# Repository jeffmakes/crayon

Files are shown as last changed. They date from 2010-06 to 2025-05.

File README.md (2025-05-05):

# Crayon
This project explores the possibility of making prototype PCB's by inkjet printing wax as an etch resist.

Check out [a talk](https://media.ccc.de/v/27c3-4099-en-file_print_electronics) I gave about the project at 27C3.

The whole printer
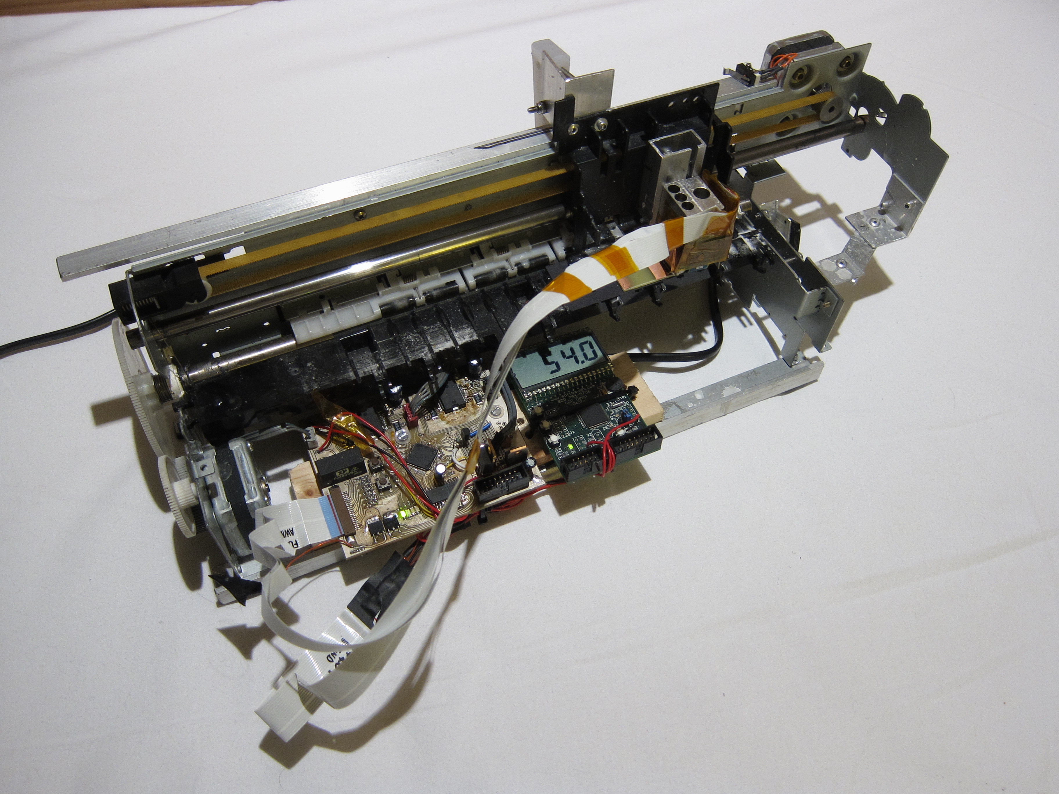
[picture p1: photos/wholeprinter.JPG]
The whole printer


Results
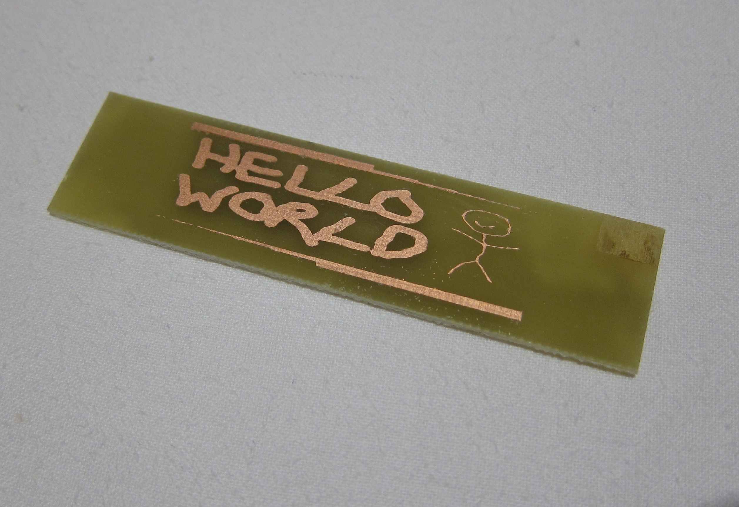
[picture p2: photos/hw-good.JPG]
Results


# Licence
The hardware designs are licensed under the CERN Open Hardware Licence Version P.
The firmware files are licensed under the MIT Licence.

# System Overview

## Motion Platform

Crayon is built on the chassis of a very old inkjet printer. It's old enough to use stepper motors for both the carriage axis and media feed axis.

## Printhead Assembly

The printhead from an Epson Stylus S21 was chosen for printing the wax. It is mounted to a custom machined heated reservoir block to hold and melt the wax. The original drive electronics from the S21 was reverse engineered, allowing a custom print controller board to be built.

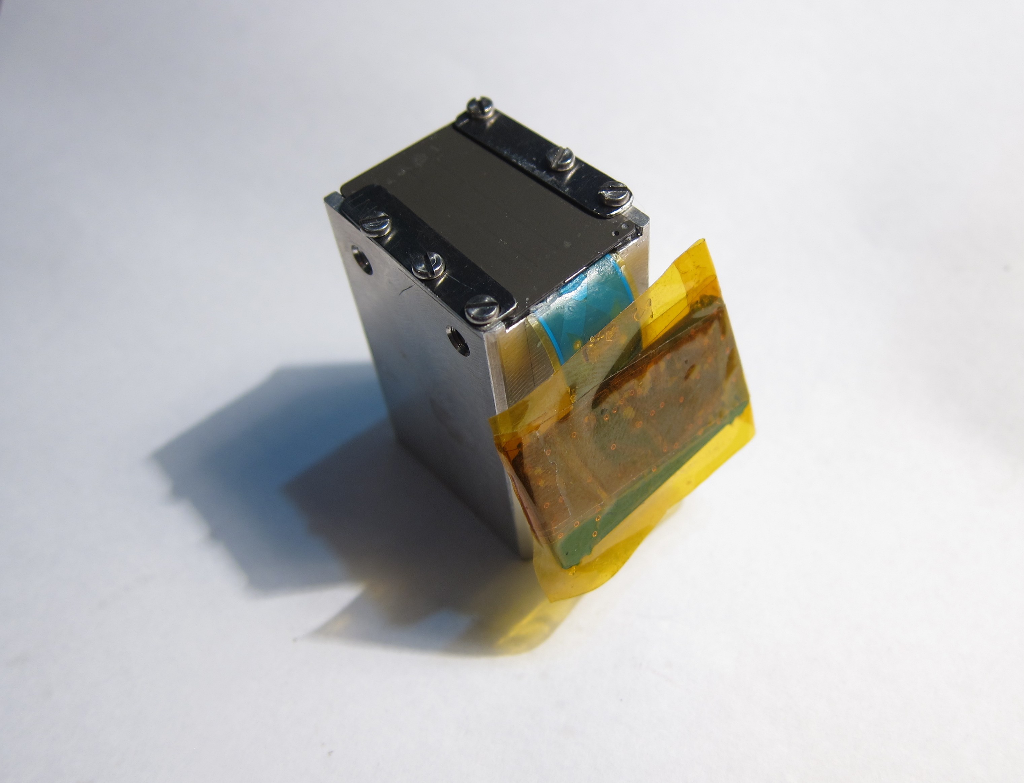
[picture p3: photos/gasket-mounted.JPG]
Printhead


## Heater

A custom heater PCB heats the reservoir block with a power transistor. A MSP430F437 microcontroller development board runs a PID control algorithm to set the temperature, and displays it on an LCD.

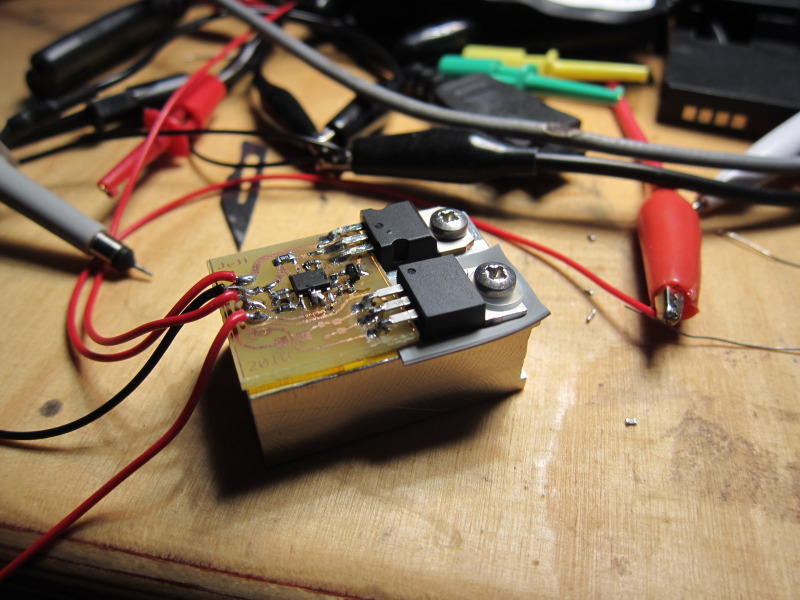
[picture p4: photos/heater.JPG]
Heater


## Controller

The heart of the printer is a custom controller PCB that generates the print data and drive waveforms for the printhead, and drives the stepper motors in the motion platform. It is based on an MSP430F2618 microcontroller. The controller is a complete replacement for the one in the Stylus S21 - the printhead interface has been completely reverse engineered, permitting full control of the printing parameters. 

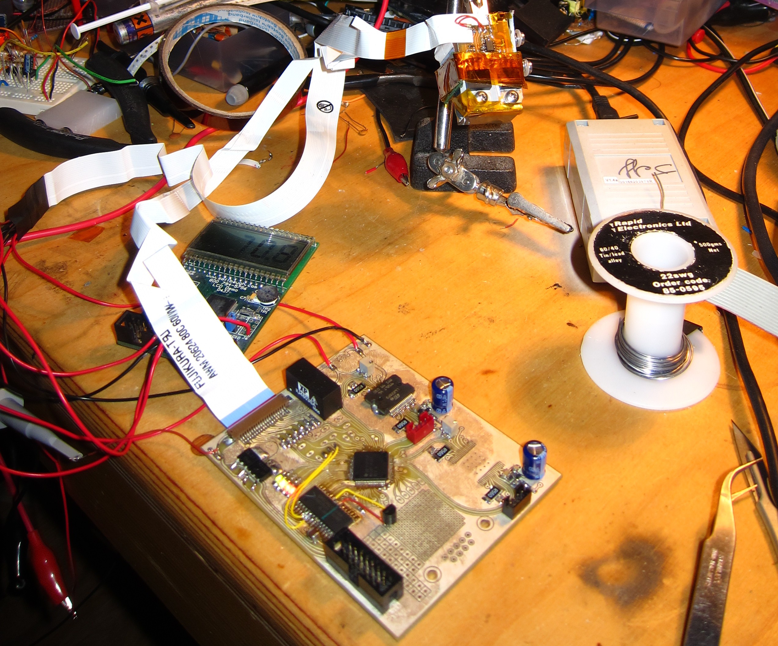
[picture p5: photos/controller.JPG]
Controller


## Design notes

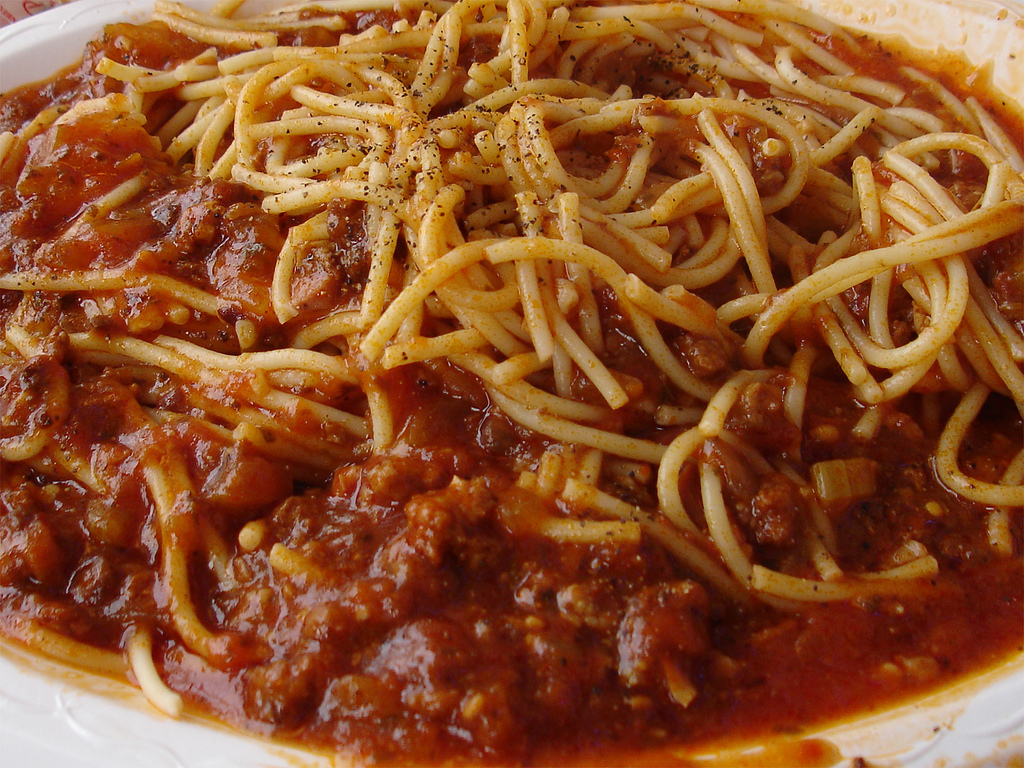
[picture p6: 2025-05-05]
photos/spaghetti.jpg

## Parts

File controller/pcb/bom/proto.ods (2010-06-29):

Part | Qty | Farnell | Description
IC1 | 1 |  | MSP430F2618TPN
IC3 | 2 | 1271000 | L6228PD Bipolar stepper Driver
D1, D2 | 4 | 1466524 | Diode 1N4148WS

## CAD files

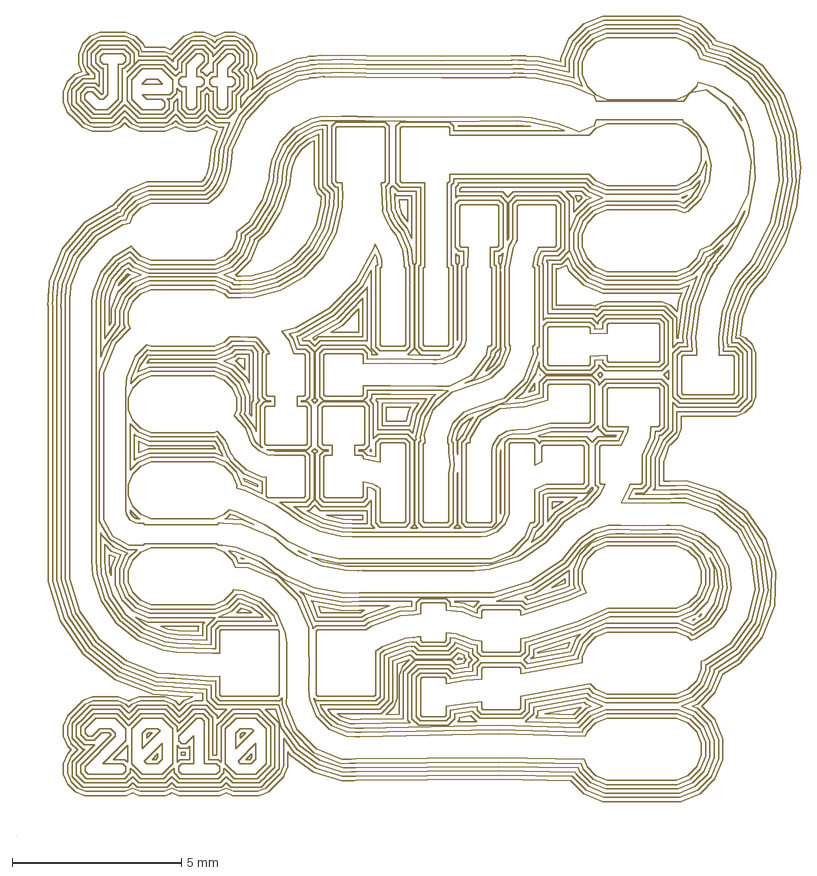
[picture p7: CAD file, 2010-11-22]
heater/pcb/heatertop.dxf
23.1 x 24.2 mm

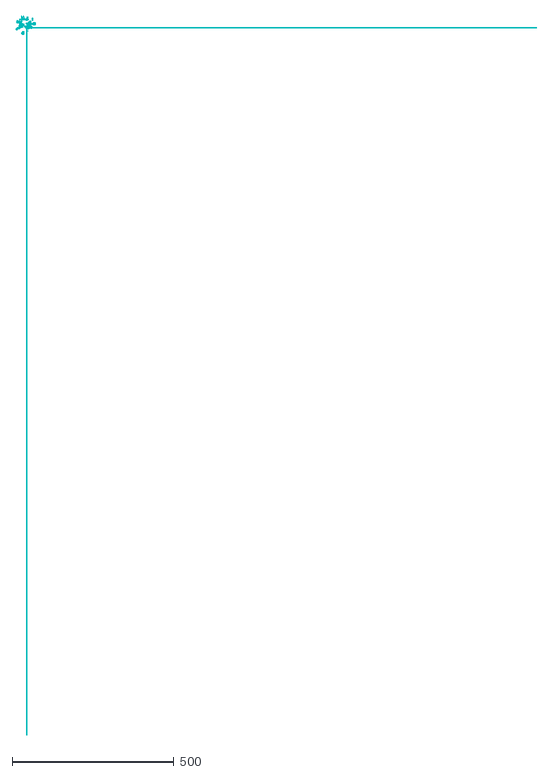
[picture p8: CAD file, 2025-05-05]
printhead-mech/paste-ungrouped.dxf
1606.8 x 2221.3

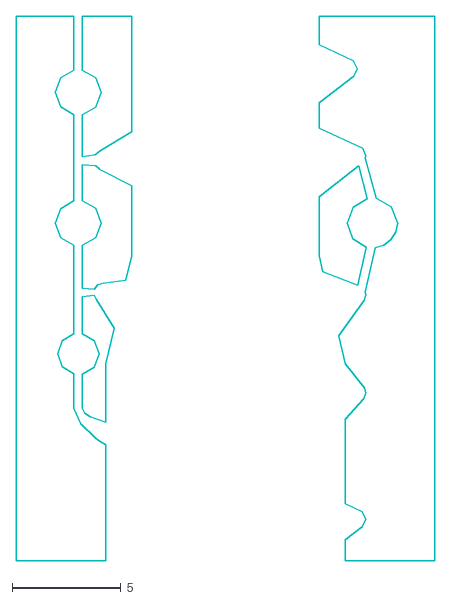
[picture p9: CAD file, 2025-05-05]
printhead-mech/gasket-mask-mirrored-2.dxf
19.2 x 25.0

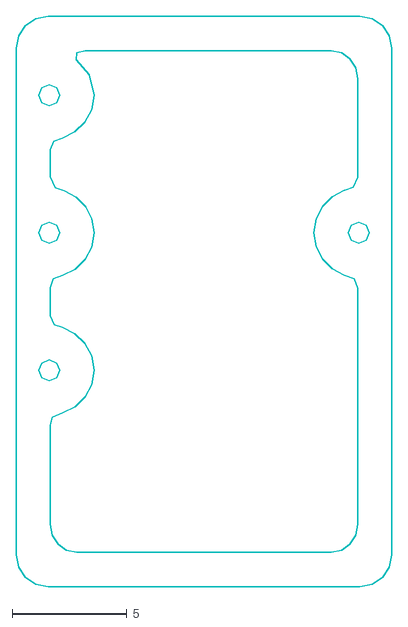
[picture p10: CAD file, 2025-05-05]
printhead-mech/rubber-gasket.dxf
16.4 x 24.9

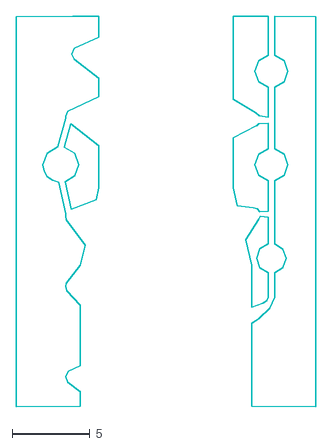
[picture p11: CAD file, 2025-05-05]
printhead-mech/gasket-mask-mirrored-3.dxf
19.2 x 25.0

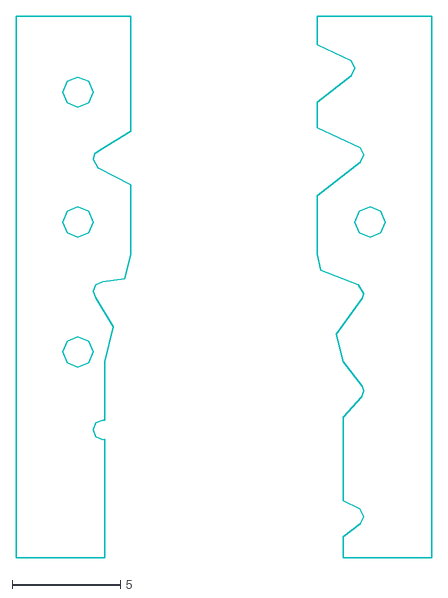
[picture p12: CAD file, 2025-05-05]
printhead-mech/tape-mk2.dxf
19.2 x 25.0

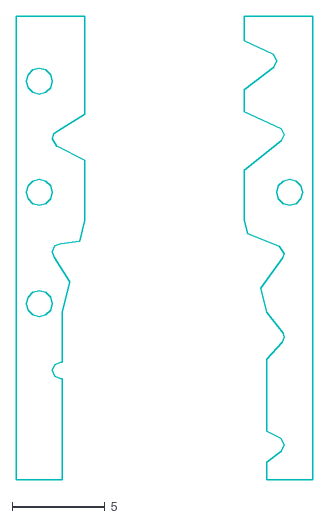
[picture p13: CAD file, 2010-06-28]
printhead-mech/tape.dxf
16.0 x 25.0

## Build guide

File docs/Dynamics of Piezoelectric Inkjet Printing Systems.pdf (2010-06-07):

# Dynamics of Piezoelectric Inkjet Printing Systems

## Shinri Sakai SEIKO EPSON Corporation Shiojiri, Nagano, Japan

### Abstract

In recent years, the inkjet technology has made great strides in the print quality. By introducing fine droplets, deep and light color inks, optimized media, and advanced color and image processing, the latest inkjet printers can produce photo-quality prints. Of these many improvements, the most contributive one is that the innovative piezoelectric print head has reduced the ink droplet size by a factor of ten in the latest five years. This innovation has been accomplished by optimizing head dimensions and driving signals as well as improving the manufacturing and assembling process. The piezoelectric actuator driven by the signal, optimized for the particular print head model, can precisely control the unrestrained ink meniscus vibration at the nozzle openings to achieve multi-sized droplets ejection in a sequent manner as well as stabilized droplet ejection up to the extremely high ejection repetition frequency. This Variable-Sized Droplet Technology (VSDT) has made it possible to introduce the digital photo-printers to the market without trading off the throughput. This paper shows how the piezoelectric inkjet technology has been improved and how much flexibility it has for particular use in home, office and industry.

### Introduction

Today, the inkjet technology has made it possible to produce high quality digital photo prints that compete against the silver halide photographs by the cooperation between the improvements of the components that constitute the inkjet technology [1] and to extend its application to wide and pioneering area by its compatibility and flexibility with digital sources.
Two types of the inkjet head technologies, one is using piezoelectric actuators and the other is using heater elements, are well known in the market. Because they have different physics and mechanism, they also have been taking different approaches to producing fine droplets. Figure 1 shows the history of the ink droplet size reduction achieved by the EPSON’s inkjet printers since its first market model in 1984. Throughout the evolution of the piezoelectric print heads, EPSON faced several difficulties in the development. Two innovative MACH technologies broke through the difficulties in 1992 and 1995 and made it possible to continue to make the successful progress. As is shown in Figure 1, the minimum droplet volume has been reduced every year and now reached 3pl. This rapid and drastic evolution, that reduced the ink droplet size by the factor of ten in the latest five years and still continues, have been making revolutions in the printing technology.
This paper will describe the structure of the inkjet heads, the dynamics of the heads, the basic approaches to generating fine droplets, and the multi-sized droplet technology accomplished by precisely controlling ink motion of the EPSON’s piezo-type inkjet printers. The application area of the piezo-type head will also be

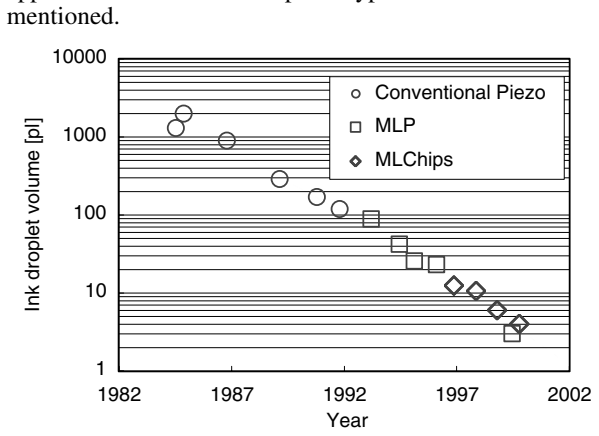
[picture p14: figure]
mentioned.; Year; Ink droplet volume [pl]; Conventional Piezo; MLP; MLChips

Figure 1. History of ink droplet volume of EPSON’s piezo type printers.

### Structure of the Piezoelectric Print Head

The piezoelectric inkjet head has a mechanism that transfers piezostriction to a volume change of the pressure chamber and this volume change induces oscillating ink flow that generates droplets from a nozzle opening. There are several types of the piezoelectric inkjet heads in terms of the mechanism of the piezo transducer.

Conventional Piezo Head
The early models since 1984 used piezo transducers similar to the head in the reference [2]. Each pressure chamber, sealed by a thin elastic plate, has a piezo strip that

IS&Ts NIP16: 2000 International Conference on Digital Printing Technologies

IS&Ts NIP16: 2000 International Conference on Digital Printing Technologies | Copyright 2000, IS&T

is narrower than the chamber width. The unimorph actuator (or vibration plate), composed of the laminate of the piezo strip and the elastic plate, transfers piezostriction to flexural deformation of the vibration plate. Figure 2 shows a plane view of the head of this type. The nozzles in a line are connected to the pressure chambers placed with large space by the long and winding channels. The manufacturing process, that puts and glues the each piezo strip on the channel substrate of plastic or glass, restricts the use of thin piezo elements thinner than about 100µm, because the piezo material is very brittle and easy to break in the process. As described later, this dimensional restriction limits the reduction of the droplets and the heads.

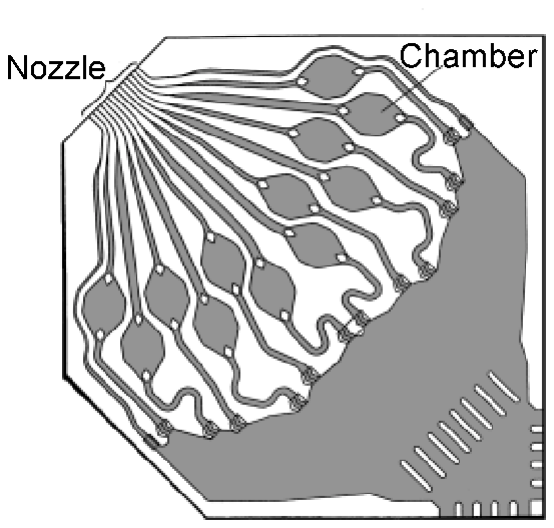
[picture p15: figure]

Figure 2. Conventional Piezo Head.

MLP (Multi-Layer Piezo) type MACH
To break through this limitation, EPSON developed new inkjet head with multi-layer piezo actuators called MLP type MACH (Multi-layer ACtuator Head), and introduced new printer with MACH in 1992 [3]. The MLP type MACH, shown in Figure 3, has multi-layer piezo elements sliced to thin pillar shape, one end of them is fixed to the base and the other end is connected to the vibration plates of the pressure chambers. This piezo element gets shorter to extend the pressure chamber by the transverse piezoelectric effect when voltage is supplied. Beside the unimorph actuator, the MLP actuator can transfer the piezostriction directly to the displacement of the vibration plate regardless of the pressure chamber size.

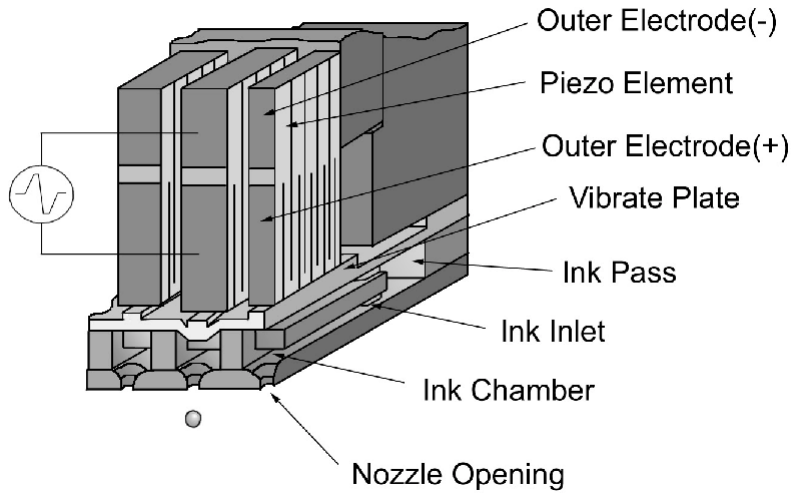
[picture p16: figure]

Figure 3. Structure of the MLP type MACH

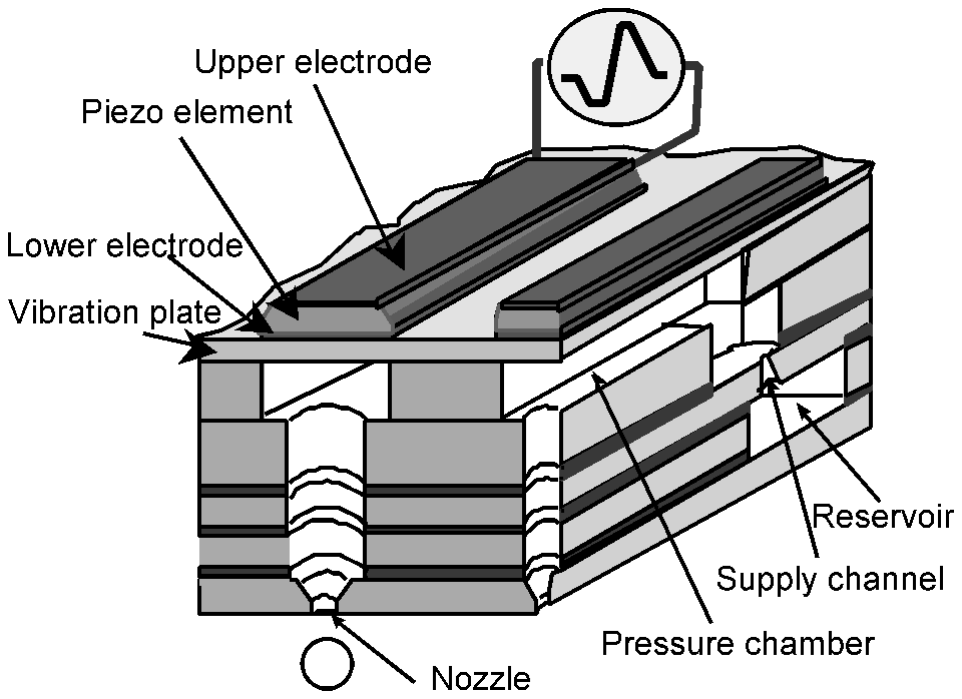
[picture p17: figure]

Figure 4. Structure of MLChips type MACH.

MLChips (Multi-Layer Ceramic with Hyper Integrated Piezo Segments) type MACH
While having high performance, the MLP type MACH costs a lot to be manufactured. To meet the market demand for low-cost and high performance inkjet printers, EPSON developed another MACH in 1995 [4]. Though the principle of the transducer, shown in Figure 4, is similar to the conventional piezo head, the piezo strips are not independently manufactured but processed and sintered together with the flow channel substrate as a single layered ceramics structure. As described later, it is strongly required to make both of the vibration plate and the piezo strip thinner to improve the inkjet head for jetting fine droplets. By taking the process that unifies the core parts of the head without machining and gluing, the MLChips could break the barrier, which the conventional piezo heads had, to develop the high cost performance printers by reducing the head dimensions.

### Dynamics of the Print Head

Understanding the motion of the actuator and the ensuing ink flow, which are actually coupled each other, and precisely estimating the parameters that define and characterize the motion, the accurate design can be done to meet the fine droplet target. In this section, the basic analytical models for the estimation of the inkjet head’s response will be explained and the responses to the simple basic inputs will be shown. Then, the relations between the analytical models and design parameters, and the strategies to the design for generating micro droplets will be described.

Analytical models for the piezoelectric inkjet heads
The channel flows that interact with the actuator as inkjet heads do are well explained by the acoustic model that takes volume velocity and pressure as independent variables. Each component of the inkjet head, such as nozzle, pressure chamber, and vibration plate, is expressed in terms of acoustic impedance, composed of inertance, compliance and acoustic resistance, and is put together in electric circuit as a equivalent model of the inkjet system. Figure 5 shows the simple equivalent circuit model for the MLChips type MACH, which uses unimorph actuator, and two major vibration modes. The mode in Figure 5(b) is the vibration mode of the pressure chamber connected to the compliance of the chamber that results in ink droplet ejection from the nozzle. The mode in Figure 5(c) is the vibration mode of the ink supply flow connected to the capillary force at the nozzle meniscus that manages the frequency characteristics of the droplet ejection.
Figure 6 shows the equivalent circuit model for the MLP type MACH. The longitudinal vibration actuator of MLP has high rigidity and can actuate the vibration plate forcibly. Add to the vibration modes of the pressure chamber (Figure 6(a)) and the ink supply flow (Figure 6(b)), there is the vibration mode of the MLP (Figure 6(c)).

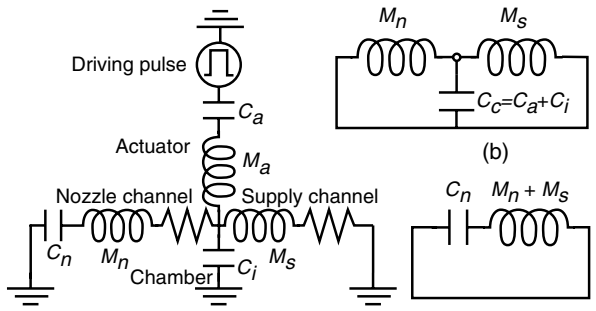
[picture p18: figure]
Nozzle channel; Supply channel; Chamber; Driving pulse; Actuator

(a) (c)

Figure 5. Equivalent model of the MLChip type MACH.

Cn Mn + Ms

Cc=Cv+Ci

Mn | Ms

(b)

(a) Ca

Ma

(c)

Figure 6. Equivalent model of the MLP type MACH.

Meniscus control
When a drive signal is applied to the piezo element, induced piezoelectric strain generates a driving force and excites the above mentioned vibration modes. Of these vibrations, the mode of the pressure chamber and its oscillation period Tc

determine the characteristics of ink ejection. Figure 7 shows the oscillating flow at the nozzle of MLChips type MACH connected to the vibration mode of the pressure chamber in response to a drive pulse of which width is the same as the oscillation period Tc

. Figure
8 shows the response to a negative drive pulse of which width is half of the Tc

(a)

0.5

1

V/Vh

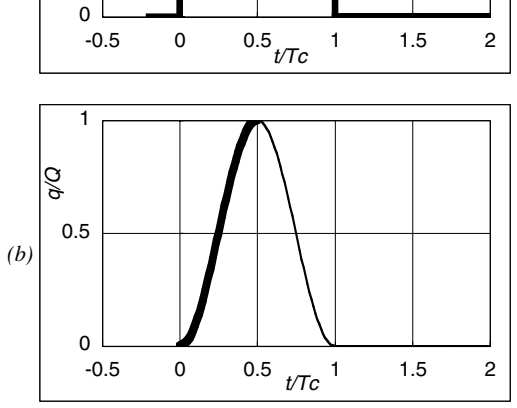
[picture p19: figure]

Figure 7. Push-Pull pulse (a) and response (b). Time in abscissa is normalized by Tc, and also voltage and flow quantity in ordinates are normalized by the pulse height and flow amplitude respectively.

The drive pulse shown in Figure 7 excites the ink oscillation that flows outward first at the preceding positive edge of the pulse, and pushes the ink at nozzle to generate a droplet. The following edge of the pulse excites the ink oscillation that flows inward first. As the following flow is in opposite phase to the preceding flow, i.e. out of phase, both flows cancel each other and no oscillation flow remains. This driving method is called Push-Pull operation. In the case of the drive pulse shown in Figure 8, the pulse width of that is half of the Tc

, an ink flow excited by
the preceding pulse (negative) edge starts to draw ink meniscus inward first, and at the time just when the ink flow begins to turn its flow direction, the following edge of the pulse generates another ink flow. Because these two ink oscillation flows are in phase, they reinforce each other, then construct a large oscillation flow, and generate a droplet twice as fast as the Push-Pull operation. This driving method is called Pull-Push operation.

(a)

0.5

1
V/Vh

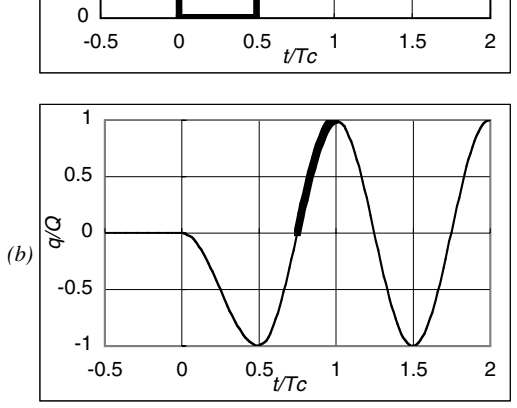
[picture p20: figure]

Figure 8. Pull-Push pulse (a) and response (b).
As well as the pulse width described above, rise-time or fall-time, in that time the pulse ramps up or down between two voltages, is also very important parameter. Compared with the sharp edge case, if the rise-time or fall-time is equal to the Tc

, no overshoot is observed in Figure 9. This pulse edge draws ink meniscus to some amount without any residual oscillations and is very useful for

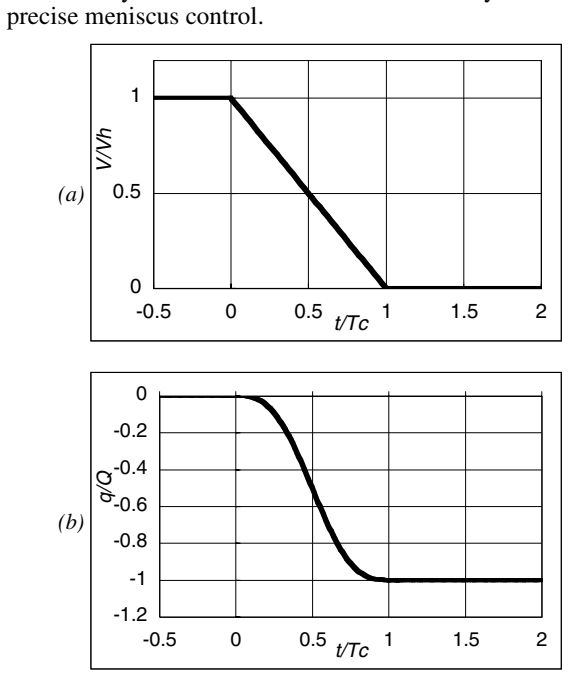
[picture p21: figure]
precise meniscus control.

Figure 9. Ramp step input (a) and response (b).

Approach to fine droplets generation
Generally, reducing the droplet volume causes slowing down the droplet speed. In the shuttle type inkjet printers, the inkjet head ejects droplets while moving fast, so the slower droplets degrade dots positioning accuracy and resultant image quality. Accordingly, the way to the faster droplets is exactly the way to the smaller droplets.
The droplet velocity is estimated by integrating ink momentum going out of the nozzle and then dividing the figure of the momentum by the droplet mass. In the case of the Push-Pull operation, integrating the flow, thick line in Figure 7, gets the droplet velocity Vm as

2
4 m
c

Q V
TA
π= | (1)

where Q is the droplet volume and A is the area of the nozzle aperture. And the oscillation period Tc

is
T | MC c | c = 2π | (2)

where Cc

is the compliance of the pressure chamber and M is total inertance of parallel connection of the nozzle and supply ink channels.
From Equation (1), the smaller the oscillation period Tc and nozzle become, the faster droplets eject. Although it helps the droplets to speed up, reducing the nozzle size causes clogging up of the nozzles, so it is difficult to make use of that. On the other hand, from Equation (2), the oscillation period Tc

is proportional to the square root of Cc

,
and as the Cc

is strongly influenced by the dimension of the vibration plate, reducing the chamber compliance is very effective to shorten the oscillation period Tc

In principle, the compliance of the vibration plate is proportional to the 5th power of the vibration plate width and is inversely proportional to the 3rd power of the plate thickness. Add to this, in the case of the MLChips type MACH, theoretically, the volume displacement of the vibration plate driven by the same voltage is proportional to the 3rd power of the width and is inversely proportional to the 2nd power of the thickness.
By optimizing both width and thickness of the vibration plate, i.e. reducing both width and thickness, for the specific droplet size, the consistent design with the evolution of the droplet size can be made.

### Multi-Sized Droplet Technology

It is evident that small droplets size needs the large number of droplets to cover the whole media with ink. But the piezoelectric inkjet head is difficult to reduce the nozzle spacing and increase the number of nozzle in terms of cost. So if only the reduction of the droplet size is made, the print head would have to shuttle lots of times and this would result in a large drop in the throughput.
The MSDT (Multi-Sized Droplet Technology) can overcome this difficulty, ejecting differently sized ink droplets in one scanning. The number of scanning is defined by the largest droplet size the head can eject, not by the smallest.
Figure 10 shows the MSDT applied to MLP type MACH [5]. The pulse pattern from the common pulse generator, applied to each piezo transducer, has two driving pulses in one cycle, corresponding to the pixel grid point. When the switch of the piezo transducer selects the pulse part2, small droplet of 3pl would eject and form a small dot (Figure 10[C]). When the pulse part3 is selected, large droplet of 10pl would eject and form a middle dot (Figure 10[D]). In the case that both pulses are selected, the large droplet would be larger than the case D by the effect of the preceding small dot ejection, two droplets would eject and total ink volume of 19pl would form a large dot (Figure 10[E]).
In the MSDT, the drive waveform is designed so that the droplets with different sizes would have about the same velocity. While the simple Pull-Push operation would eject droplets twice as fast as the Push-Pull operation, by taking large Pull and small Push, the smaller droplet ejection was made possible.
Also in the MSDT, new idea of the Pull-Push-Pull operation, which is the combination of the Pull-Push and the Push-Pull, is implemented. The last Pull is set to cancel the previously generated flow like the Push-Pull operation. The response to this complex waveform can be easily understood by the superposition of the oscillations generated by each pulse edge.

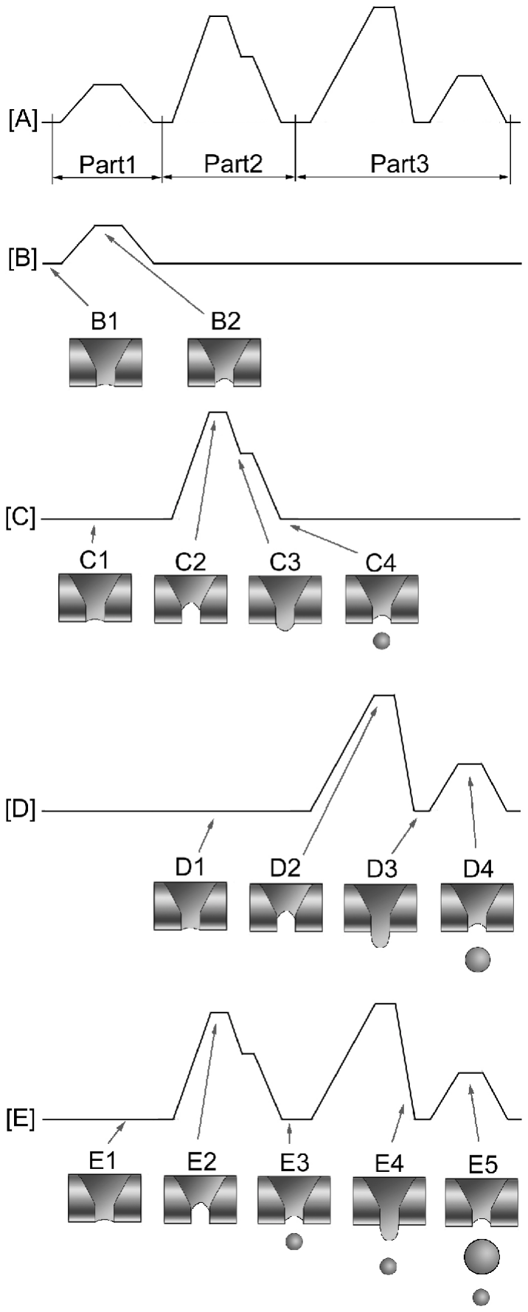
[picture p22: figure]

Figure 10. Driving waveform of MSDT

### Evolution of the Piezo Inkjet Technology

As above described, the piezoelectric inkjet head can precisely control the ink meniscus motion and change the droplet volume by means of the driving signal. This controllability made possible to adapt the inkjet heads to plenty of ink and media combinations and apply them to from the photo quality home print to the professional large format and arts.
From the viewpoint of the droplet size, if only a small droplet is pursued, it is easy to establish a new record. On the other hand, piezoelectric inkjet head can accept a variety of inks other than water base inks. These potentials can lead the piezo inkjet head to the new application area of the marking technology.

### Conclusion

The piezoelectric inkjet heads has been evolving at marvelous speed, introducing new actuators. The high linearity of the actuators has given the high controllability, and the design flexibility and ultimate optimizing technique established applicability of the piezo inkjet technology to the all sort of digital printings.

### References

1. M. Fujino, Proc. SPIE, Vol. 3963, pp. 340-348 (2000).
2. E. L. Kyser, S. B. Sears, US patent 3,946,398, (1976).
3. | T. Kitahara, Proc. IS&T’s 11th | International Congress on
Advances in Non-Impact Printing Technologies, pp. 346-349
| (1995).
4. | M. Usui, Proc. IS&T’s 12th | International Conference on
Digital Printing Technologies, (1996).
5. T. Kitahara, Japan Hardcopy ‘99, pp. 335-338 (1999).

### Biography

Shinri Sakai is a chief specialist in the Printer Development Division of SEIKO EPSON Corporation. He received his B.E. and M.E. in mechanical engineering from the Tokyo Institute of Technology, Japan, in 1983 and 1985 respectively. He worked on electrophotography system for three years and currently is working on ink jet printing system development. His primary responsibilities are mechanical and physical analysis and computer simulation for ink jet head development and optimization. His recent interests are rheological features of inks and their contribution to ink meniscus control and droplet formation.

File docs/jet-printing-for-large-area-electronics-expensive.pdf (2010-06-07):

# Jet Printing for Large Area Electronics

## Steven Ready, William Wong, Kateri Paul, and Bob Street

Palo Alto Research Center, Inc.

## Palo Alto, California

### Abstract

The advent of new solution based organic and inorganic/ organic hybrid semiconductor material along with a desire for less expensive ways to produce large area electronic devices has stimulated research into non-conventional circuit patterning methods. We report on an inkjet based printing system which was constructed to facilitate the production of etch masks and electronic devices for large area applications such as displays and x-ray sensors. A multi-ejector wax print head was integrated for high accuracy, high throughput printing of etch masks and material exclusion zones in the processing of amorphous silicon and organic electronics circuitry. The same system also utilizes specialized single ejector print heads to deposit a wide variety of organic electronic materials for rapid turn experimentation required for materials and process development. Feature sizes down to 20µm and control of feature placement below 5µm are achieved. System design and capability will be discussed in the context of the resolution, throughput, material requirements and electronic device performance.

### Introduction

Recent developments in solution based organic electronic materials have encouraged efforts in exploring the use of conventional printing methods to produce very low cost electronic devices.¹⁻⁴ Confidence in the early maturing of this technology has spawned the creation of several companies vying for an early adaptor’s advantage in market share and name recognition.⁵
Among the initial applications sited are radio frequency identification (RFID) tags and displays. The potential advantage for RFID tags is to produce these small devices at such a low cost that they will replace bar code scanning and enable many more uses. While largely driven by the desire to integrate newly developed organic LED material, the application of printed organics to display manufacture can also be seen for its potential to greatly reduce the equipment cost, increase the throughput and provide the capability to use inexpensive flexible substrates. The Holy Grail for this technology is the realization of integrated electronics without the need for expensive vacuum deposition, etching, and lithography equipment. There are several methods borrowed from current document printing technology that can be applied to the patterning solution based organics.⁶,7 Two of the most quoted methods are ink jet and stamping. While, jet printing is perhaps the most flexible in terms of the variety of materials and modifications to the design, most reports to date focus on single ejector applications. In most applications to large area electronics such as displays, the throughput bottleneck imposed with the use of a single ejector is prohibitive. The need for high throughput offered through parallel deposition methods without sacrificing alignment, accuracy and repeatability is crucial for this technology to succeed in applications from large area imagers to flexible displays to active/passive flex circuitry to distributed sensors on a flex medium.
Here we discuss a research system for jet printing material to produce electronic devices and circuits. Our intent is to explore new materials and processes as well as flesh out the issues for the development of a high throughput, highly reliable large area jet printing system.

### System Description

The printing system consists of a high accuracy XY stage fitted with two temperature controlled vacuum chucks for substrate transport, a multi ejector wax piezo print head, and two varieties of single ejector print heads used for the application of organic electronic material. All of the print heads were taken from other print related projects and as such were not designed for this purpose. The system is also fitted with two miniature video microscopes position registered to the various print heads for alignment and verification purposes.
The system electronics are comprised of National Instruments digital IO and waveform generator PC cards capable of printing up to at 40 kHz, or 1 m/sec at 600dpi. The XY stage control electronics supply positioning and ejector triggering to an accuracy of 0.1 µm.

Wax Printing
The wax multi-ejector printhead consists of several hundred staggered piezo ejectors. The print head and wax reservoir are heated above the wax melting point of 80°C. While the wax reservoir and fluidic delivery system in the print head was designed to print horizontally, in this application the printhead is positioned over the XY stage and prints downward onto the substrate. A Kemamide based wax is ejected using waveform parameters beyond those normally specified for document printing. The resulting spot sizes are approximately 40 µm diameter. To completely fill

IS&T's NIP18: 2002 International Conference on Digital Printing Technologies an area in raster fashion a minimum of 8 passes of the print head.
Under normal operating conditions for document printing, variations in spot placement can be as large as 50 µm. Modifying the waveform and wax temperature in order to produce ~40 µm spots while ejecting downward did not remarkably worsen this variation. In fact, as seen in figure 1, most of the spots were within 10 µm of the expected placement. However, these ejection conditions caused a number of ejectors either to fail to eject or fail to continuously eject. This situation is made worse by the fact that a number of ejectors work or fail to work after thermal cycling. In order to provide a robust system which produced reliable ejection during a printing session as well as ~1 µm spot placement accuracy, a machine vision spot placement/ calibration procedure was implemented as well as a method for printing with a sparse set of ejectors. The calibration routine also allows us to extract and correct for variations due to head angular misalignment, thermal expansion of the head that can result in a run out error of up to 25 µm and an offset error which results from the time it takes for the drop to travel to the moving substrate. While the hardware has the potential to correct for variations of individual ejector drop velocity, we have not attempted to implement this yet.

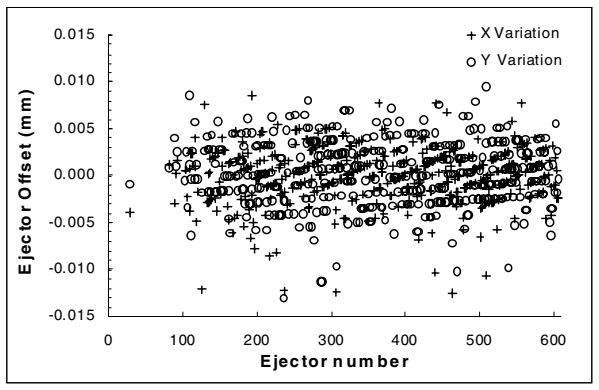
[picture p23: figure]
Ejector n um ber; E jec to r O ffs et (m m ); X Variation; Y Variation

Figure 1 Variation in X and Y spot placement for the 424 working ejectors. Spots producing greater than 15 variations not shown

With the methods outlined above, spot placement is controlled to within ±1 µm. While the reduction in the number of available ejectors on the head reduces the amount of parallelism achieved, the average time it takes to print a mask layer on a 4-inch wafer is measured in fractions of minutes rather than the tens of minutes it would take for a single ejector.
Figure 2 shows a segment of an array of transistors fabricated from jetted wax mask layers of amorphous silicon/metal/dielectric material. The transistor cells are 320 µm square and perform as well as transistors fabricated from standard photolithography. For each mask layer, the single printed mask step replaced 4 standard lithography steps; spin on resist, oven bake, mask align and expose, and strip. This method also allows for on the fly design modifications.

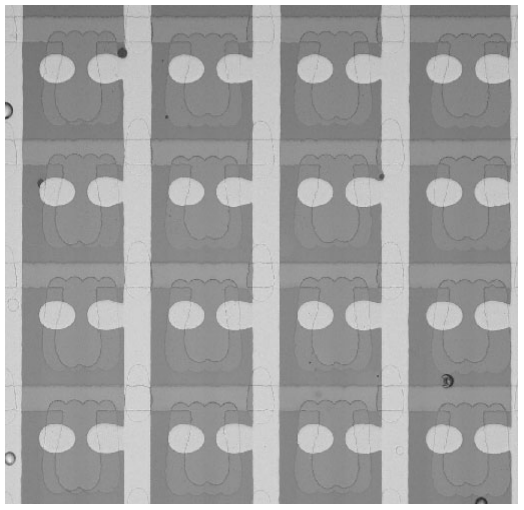
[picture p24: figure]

Figure 2. Jet printed wax mask defined amorphous silicon transistors on 320 µm array grid.

Single Ejector Solution Printing
Single acoustic and piezo ejectors are used to print organic electronic materials onto test circuits. In order to accommodate the variety of materials to be printed, the simple ejectors eject up onto the substrate that are fixed to a temperature controlled vacuum chuck.
The acoustic ejector⁵
(figure 3) consists of a piezo material bonded to a quartz lens submersed in the fluid to eject. The lens transmits high frequency (100-140mHz) acoustic energy and focuses the energy at the fluid surface resulting in the ejection of a drop. Similar devices have controllably produced variable drop volumes from 1 femtoliter to 10 nanoliters, with control of ± 2%.

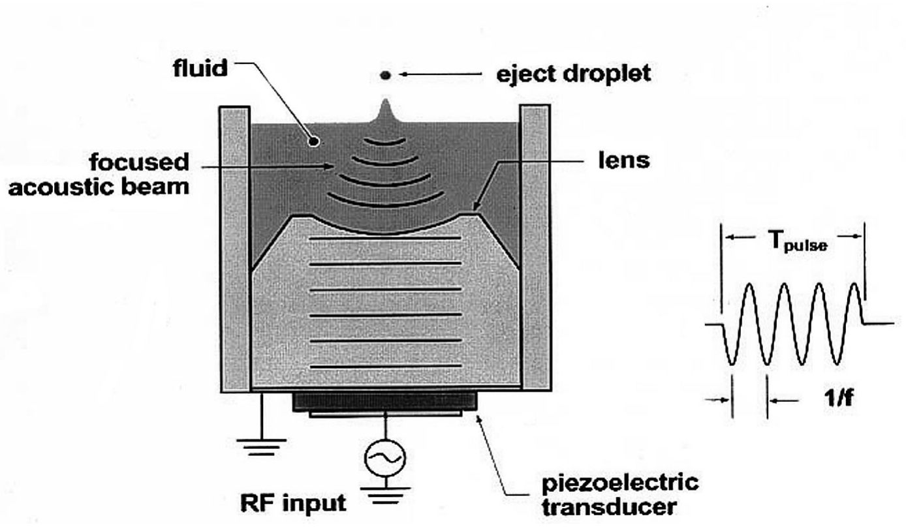
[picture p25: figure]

Figure 3. Acoustic single ejector schematic. The focused RF acoustic energy ejects droplets from free fluid surface

The advantage of this ejector system is the ability to eject from a relatively free fluid surface. Many of the polymers of interest are dissolved in volatile solvents (i.e. xylene, toluene), some of which require modestly elevated temperatures to maintain the polymer in solution. The availability of any free surface from which solvent can evaporate tends to build up polymer concentrations, forming a film at the fluid surface. Small nozzle apertures tend to clog while the nozzle-less surfaces survive better, particularly under relatively constant ejection.
The piezo single ejector (figure 4) in use is of all stainless steel construction with reservoir volumes as small as 20 microliters. This ejector is intended to be used initially for relatively precious material under investigation. Variations in design parameters allow for drop volumes range from 50 picoliters to 10 nanoliters, with control of ± 2% and fluid utilization of 95%. Due to the small aperture, it is more useful for less volatile solvents and water-based solutions.

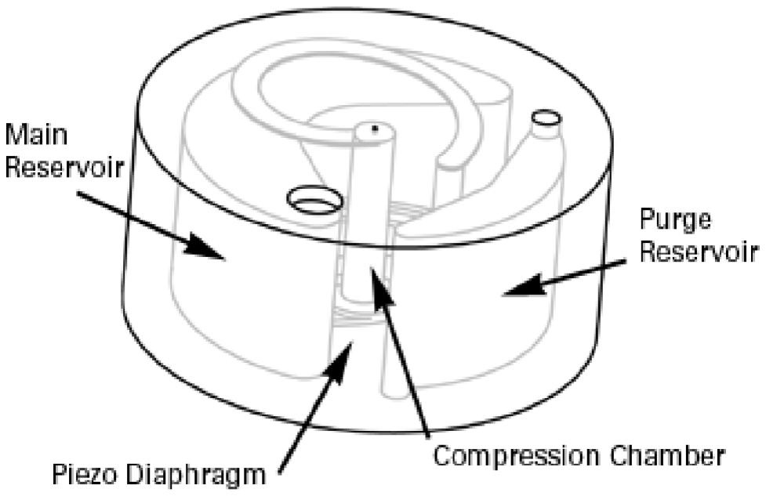
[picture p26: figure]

Figure 4. Single piezo ejector design. The self-contained reservoir/ piezo/aperture unit is approximately 1cm in diameter.

Materials Printing
The printing of the variety of materials on the variety of surfaces poses a significant challenge to systems designers as well as researchers in the field. Feature size definition relies on control of the deposited material that can be predicted and optimized for a given ejected material on a particular surface. However, electronic devices usually require several different surface layers interacting with the material being deposited, either favorably or unfavorably. The deposition conditions to produce well-defined features can conflict with the electronic performance of the materials. For instance, a solution of F8T2 in xylene, which needs to be heated to ~40°C in order to keep the polymer in solution, deposits into well-defined structures on a ~40°C heated substrate. However, the time it takes to evolve the xylene at this temperature does not allow the F8T2 to order, producing a poorly performing transistor with carrier mobilities 1-2 orders of magnitude lower than optimal material. Deposition of F8T2 on a room temperature substrate produces acceptable electronic behavior, but the deposition of consecutive drops produces coalescence and area dewetting, forcing the time between consecutive drops (to allow for solvent evaporation) and thus print speeds to potentially unacceptable values. As an example of this effect, Figure 5 shows two lines of PDOT, a conductive polymer, deposited on BCB, a polymer dielectric, at different printing speeds.

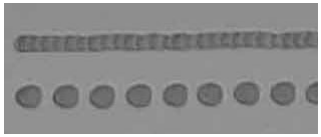
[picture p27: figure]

Figure 5. PDOT deposited on BCB. The bottom line was printed faster than the top line showing the effect of liquid surface tension overpowering surface wetting.

In organic as well as most other electronic materials, barriers to carrier transport such as of grain boundaries and regions of disorder are highly undesirable. Conditions that promote the formation of homogeneous material during sequential droplet deposition enhance the electrical performance. The use of coalescence, surface engineering, viscosity, solvent volatility and liquid surface tension with substrate temperature and printing speed can produce uniform lines of material with directionally enhanced performance. Figure 6 compares transfer characteristics of two transistors where the F8T2 is deposited parallel and perpendicular to the source and drain electrodes.

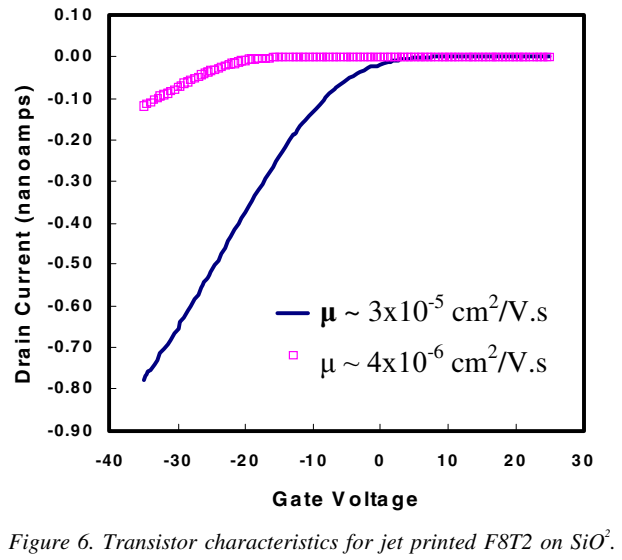
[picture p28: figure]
G ate V olta ge; D ra in C urrent (nan oa m ps); cm² /V.s; ⁻⁶ cm² /V.s

Figure 6. Transistor characteristics for jet printed F8T2 on SiO² The solid line shows characteristic for F8T2 jetted perpendicular to the current direction. The boxes are from F8T2 jetted parallel to the current direction.

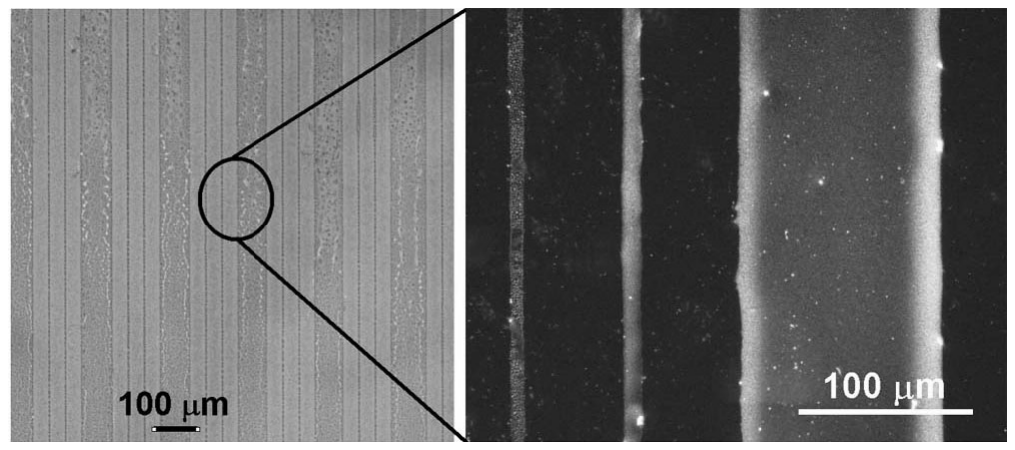
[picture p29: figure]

Figure 7. Wax patterned self-assembled monolayer of OTS dip coated in a florescent dye. The black areas are the wax patterned OTS. The thin florescent lines are 5-8 µm wide.

In order to circumvent and perhaps simplify the problems associated with jet printing solution-based organics, methods based on engineering of surface energies have been developed.⁸
Patterned self-assembled monolayers (SAM) have been used to organize surfaces into hydrophilic/hydrophobic areas. The solution based organic electronic material can then be dip coated, thus only adhering to the hydrophilic areas. Figure 7 shows an example where a octadecyl trichlorosilane (OTS) was applied to an SiO2 substrate. The substrate/SAM was patterned by jetting wax. The exposed SAM was then removed from the surface prior to the wax removal. The entire wafer was then dip coated with a florescent dye that dewetted from the patterned OTS surfaces. In this way, feature sizes much smaller than the wax drop size can be achieved and only depend on the control of the wax drop size and placement.

### Conclusion

An ink jet printing system consisting of a multi-ejector wax printhead and single ejectors for electronic polymers was presented. Methods for achieving spot placement accuracy using the multi-ejector head was discussed and accuracies of ± 1 µm were achieved. Examples were given on how print direction, surface properties and other parameters affect the control of features and performance.

### Acknowledgements

We would like to acknowledge the contribution of Rick Stearns, Babur Hadimioglu and Scott Elrod for their help with the acoustic jet printing as well as Bob Krivacic, Bob Kowalski, Dave White and Bob Matusiak for their contribution to the development of the print system.

### References

1. Garnier, F., R. Hajlaoui, et al. (1994). "All-polymer field-effect transistor realized by printing techniques." Science 265(5179): 1684-6
2. Bao, Z., Y. Feng, et al. (1997). "High-performance plastic transistors fabricated by printing techniques." Chemical Materials 1997(9): 1299-1301
3. A few of the companies are Add-Vision, Plastic Logic, UNIAX, Universal Display
4. Wong, W.S.; Ready, S.; Matusiak, R.; White, S.D.; Lu, J.-P.; Ho, J.; Street, R.A., APL 80, 610 (2002)
5. S. Elrod, C. Brown, S. Buhler, R. Ellson, J. Fitch, B. Hadimioglu, R. Kowalski, R. Matusiak, J. Roy, D. Ruiz, B. Russo, R. Sprague, M. Weisburg, D. White, M. Young, and J. Zesch, IS&T NIP17 Proc. 669 (2001)
6. Hsin-Hua Chang; Chung-Chih Wu; Cheng-Chung Yang; Chieh-Wei Chen; Cheng-Chung Lee, Proc. SPIE - Int. Soc. Opt. Eng. (USA) 4079, 127 (2000)
7. Speakman, S.P.; Rozenberg, G.G.; Clay, K.J.; Milne, W.I.; Ille, A.; Gardner, I.A.; Bresler, E.; Steinke, Org. Electron, 2 65 (Sept 2001)
8. H. Sirringhaus, T. Kawase, R. H. Friend, T. Shimoda, M. Inbaskaran, W. Wu, E. P. Woo, Science 290, 2123 (2000).

### Biography

Steve Ready obtained his degree in Physics from the University of California at Santa Cruz in 1984. He then joined Xerox Palo Alto Research Center and has since studied the role of hydrogen in amorphous, polycrystalline and crystalline silicon, contributed to the development of large area amorphous and polycrystalline silicon imaging arrays for optical and x-ray applications, and is presently working on the development of organic semiconductor materials and devices.

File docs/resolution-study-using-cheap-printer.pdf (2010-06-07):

353

# Inkjet Printing Resolution Study for Multi-Material Rapid Prototyping∗

Mustaffa IBRAHIM∗∗, Takayuki OTSUBO∗∗, Hiroyuki NARAHARA∗∗,

Hiroshi KORESAWA∗∗ and Hiroshi SUZUKI∗∗

In addition to its application in media printing, inkjet printing is becoming an increasingly attractive option for the distribution and patterning of materials for a wide variety of applications. In this study a commercial inkjet printer was modified to study the resolution of fluid dot placement required to fabricate 3D multi-material patterns layer by layer. A Javabased computer program was developed to convert stereolithography (STL) data layer by layer, control ink cartridges individually and print ink with customized fluid dot placement arrangements. The study found that complement printing between nozzles which are 30 µm in diameter and 144 µm apart is essential to achieve a sufficiently dense 3D pattern. When printed with 36 µm vertical spacing a layer thickness of 1.30 µm is achievable, and when printing layer by layer, the thickness increases almost at a linear rate.

Key Words: Rapid Prototyping, Inkjet Printing, Multi-Material, Resolution, Positioning

### 1. Introduction

The advancement of manufacturing technologies is being driven by the need for automation, miniaturization, cost reduction and environmentally friendly manufacturing. The prospect of adopting inkjet printing technology in various advanced manufacturing processes is very promising. With this broader view of the technologies encompassed by the term “inkjet printing”, applications in electronics, optics, displays, virtual reality, medical diagnostics, and medical procedures have been developed using inkjet fluid microdispensing as an enabling technology⁽¹⁾. This study intends to utilize a Java program to manipulate CAD design data and interface them with a modified commercial 357-nozzle piezoelectric printer to produce 3D patterns, as shown in Fig. 1.
1. 1 Fabricating 3D structure using inkjet printing Recently a rapid prototyping method for building parts layer by layer has led to interest in fabrication of electrical circuits and optical devices by inkjet printing. The classic definition of rapid prototyping is “a special class of machine technology that quickly produces mod-

∗ Received 28th October, 2005 (No. 05-4226) ∗∗ Department of Mechanical Information Science and Tech-

nology, Kyushu Institute of Technology, 680–4 Kawazu, Iizuka-shi, Fukuoka 820–8502, Japan.
E-mail: nara@mse.kyutech.ac.jp

els and prototype parts from 3D data using an additive approach to form the physical models”⁽²⁾. The characteristic feature of the inkjet process is to print dots, but for printing multi-material 3D functional parts, lines and areas with good dot-to-dot conductivity are a necessity, as for example in electrical and thermal conduction applications. An inkjet printer patterns material by ejecting tiny droplets of liquid ink from its printhead nozzles or orifices as it moves in two dimensions approximately 1 mm above a substrate. The advantages of inkjet technology are straightforward: its apparent simplicity, the fact that it is data-driven, its high material deposition speed, reduced waste of costly materials, and elimination of cross-contamination on surfaces because it is a noncontact process. The overall size of the particles that can be jetted are limited by the diameter of the nozzle exit ori-

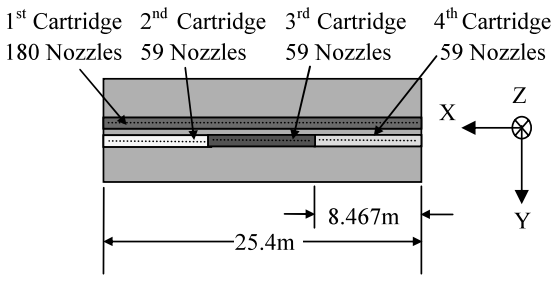
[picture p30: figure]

Fig. 1 Piezoelectric printhead configuration

JSME International Journal | Series C, Vol. 49, No. 2, 2006

354

Fig. 2 Single channel drop-on-demand dispensing device configuration

fice diameter, and line width/thickness is determined by the jetted liquid properties and the orifice diameter⁽³⁾.
1. 2 Related studies
Although there is already ongoing research into using inkjet printing to build MEMS, organic displays, and biological arrays⁽⁴⁾, (5), most systems use a drop-on-demand platform that has a single-nozzle piezoelectric-actuated device, such as that from MicroFab Technologies Inc.⁽⁶⁾, to direct write materials, as denoted in Fig. 2. The Z Corp. rapid prototyping machine, which uses 3D printing technology originally developed at the Massachusetts Institute of Technology, has traditionally used plaster and resin powders onto which an inkjet printer sprays glue to create solid prototypes, and cellulose fiber bound with an adhesive for creating models used for investment and sand castings⁽⁷⁾. Objet Geometries Ltd. has successfully inkjet photopolymer to create models, using multiple nozzles to jet layer on layer of photopolymer, with each layer cured immediately by exposure to UV light⁽⁸⁾. Even though inkjet printing technology has been used to fabricate 3D structures or models, parts produced by the commercially available rapid prototyping systems are made of a single material. The multi-color 3D printer from Z Corp. only prints colors on surfaces — the material beneath is still the same as the modeling material. In other rapid prototyping systems, various parts are built independently using different colors and then assembled at a later stage. A new system is expected which can produce assemblies composed of parts with more than one color or with more than one material⁽⁹⁾. With this capability, some post-processing of rapid prototyping such as assembly, bonding, welding and painting can be eliminated. Drop-on-demand inkjet technology is among the rapid prototyping methods that can be extended to build multi-material assembly by adding more material inkjet nozzles to deposit materials selectively, layer by layer.
In our previous study, silver nanoparticle ink which contains silver, plated gold, tetradecane as solvent and has a particle size between 3 and 7 nm was successfully printed using inkjet printing technology to directly write an electronic circuit as depicted in Fig. 3. The results also show that the environment and ink curing temperature have a strong effect on the silver ink viscosity and volume resistivity as shown in Figs. 4 and 5. Due to these differences, it is not easy to get the same printing results as with the original ink. Conductive lines measuring 100 µm

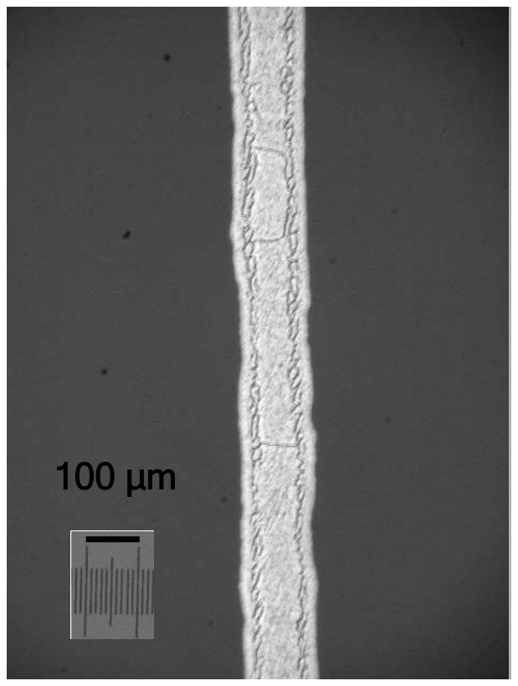
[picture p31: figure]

Fig. 3 Printed silver ink

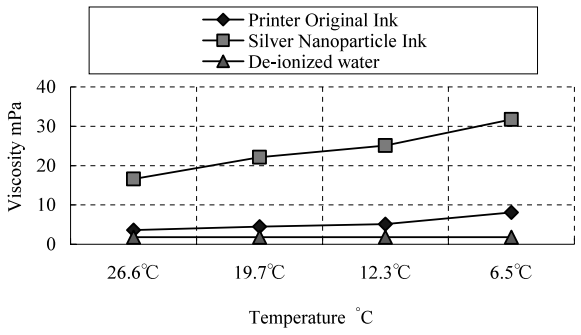
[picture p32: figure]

Fig. 4 Temperature effect on viscosity

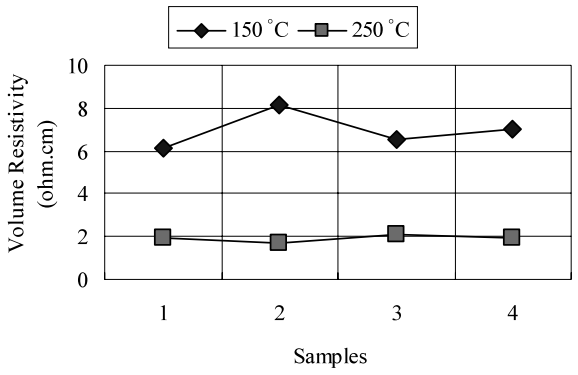
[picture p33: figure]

Fig. 5 Temperature effect on volume resistivity

in width were printed with the printer, and after curing the solvent evaporates, causing the silver ink to lose about 20% of its volume, leaving the silver ink with a width of 80 µm⁽¹⁰⁾.

### 2. Materials and Methods

The focus of the experiments was to study the area covered by deposited ink horizontally and vertically in order to print 3D patterns. Although in our previous study, silver nanoparticle ink was successfully printed and can

Series C, Vol. 49, No. 2, 2006 | JSME International Journal

355

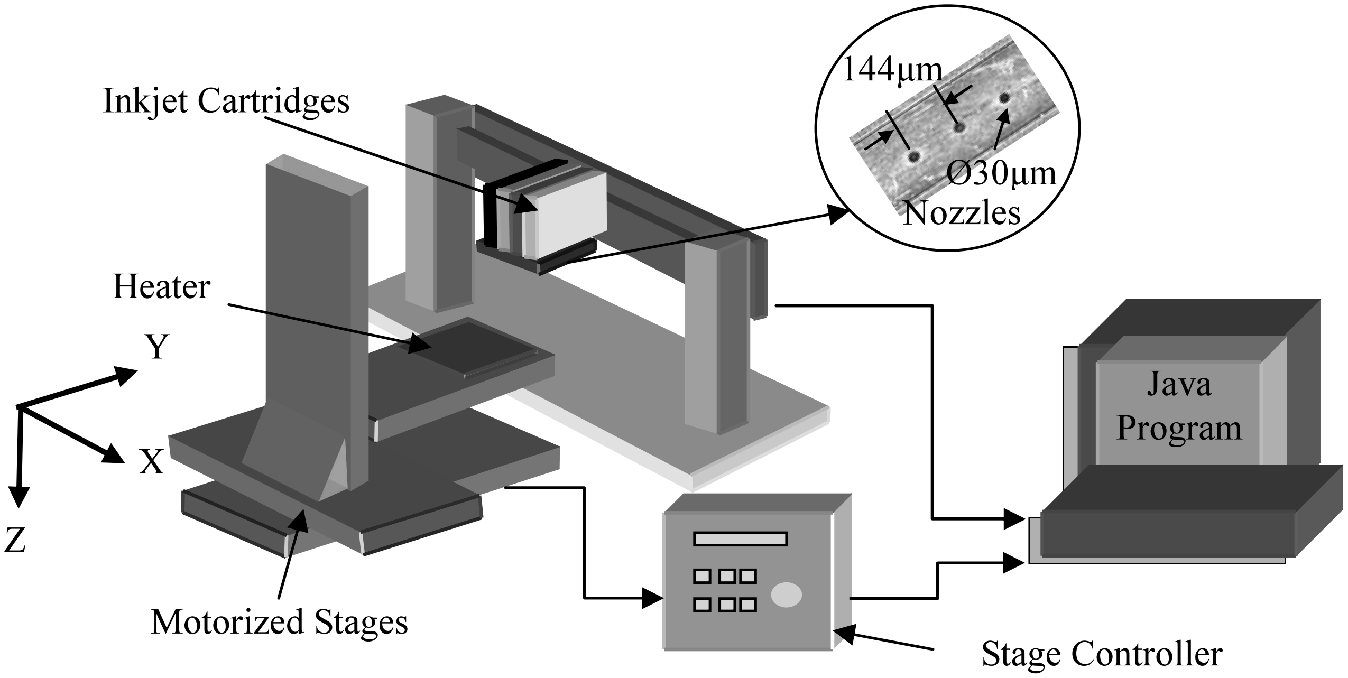
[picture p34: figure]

Fig. 6 Inkjet printing system

function as a conductive circuit, a more thorough understanding of printer capabilities in arranging dots in both the X and Y axis and in patterning 3D patterns needed to be reached. A Java program was developed because of limitations in using the window based printer driver software. Among the printer software limitations are:
- Several nozzles will be depositing simultaneously when image data was sent and this will create problem in fabricating multi-material 3D structure.
- The paper feeding mechanism distance movement cannot be customized when complement printing is required.
- Synchronization between printing and motorized stages cannot be done due to different operating window. The Java program developed in this study is capable to:
- convert from CAD data to pixel image data
- direct control the printer bypassing the printer software
- independently control the fluid cartridges selection
- synchronize motorized stages and printing movement
The present study used the printer’s original pigment ink, with a surface tension of approximately 28.7 mN/m and viscosity at room temperature of approximately 3.59 mPa⁽¹¹⁾. The ink cartridges were mounted on a commercially available desktop printer that was modified to be capable of fabricating 3D patterns layer by layer. The positioning of deposited ink is important because failure to deposit ink in some areas would have a significant effect if functional inks such as conductive or magnetic ink were to be used.
2. 1 Drop-on-demand inkjet systems
Among the numerous types of inkjet technology, the most common are drop-on-demand systems such as thermal and piezoelectric, which have dominated the lowerend printer market. In thermal inkjet technology, the drop is initiated by heating the ink to create a bubble until pressure forces it to burst and hit the paper. However, the high temperatures may trigger problems or incompatibilities with certain functional ink formulations. The other inkjet technology used in this study is from Epson, and utilizes a piezoelectric crystal positioned at the rear of the inkjet reservoir. When actuated, the piezoelectric crystal flexes and forces a drop of ink out of the nozzle⁽¹²⁾.
2. 2 Experimental setup
This study used a Java program to slice rapid prototyping STL data and translate them to bitmap data layer by layer. The layer image was then sent to the printer, which was also controlled by the Java program, so that it was feasible to choose the inkjet cartridge individually for color selection and to avoid the color mixing process which the printer software would initiate under normal operation. The modified printer was equipped with motorized stages and a heater in order to fabricate 3D patterns. The inkjet printing system’s horizontal movement is not modified, but the mechanical paper feed mechanism was replaced by motorized stages as depicted in Fig. 6. The Java program synchronizes movement of the motorized stages with the printer in order to fabricate 3D patterns identical to the rapid prototyping concept. A film heater was placed on top of the stage to dry the deposited fluids and maintain their shape rather than allowing them to spread out on the surface, which would cause dots to interact with one another. The printer’s printhead nozzle is about 30 µm in diameter and the distance between nozzles is 144 µm. A summary of the conditions under which the experiments were carried out is given in Table 1.
2. 3 Ink drying and spreading
First, the ink drying temperature had to be determined, because partial drying would cause the ink to appear dry on the surface while trapping solvent underneath. A film heater was used, and the voltage supplying it was varied to ascertain the time and temperature required to dry the ink. To make sure heat was evenly distributed, a

356

Table 1 Experimental conditions

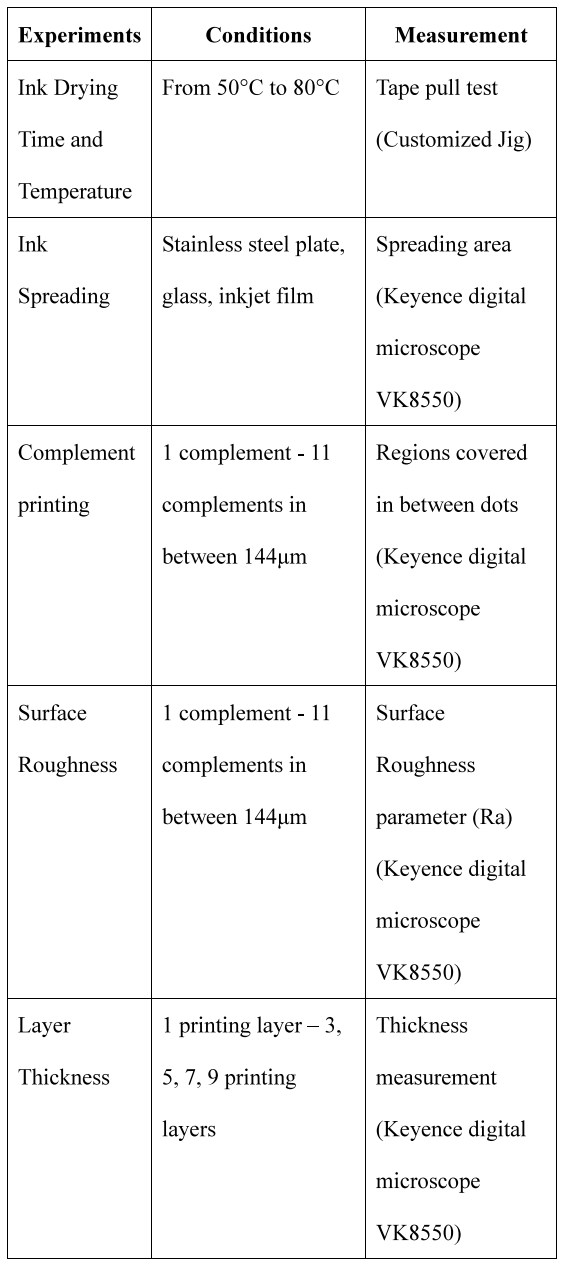
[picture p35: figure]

copper plate was placed on top of the heater. A tape pull test was then performed to make sure that the ink was adhering well to the substrate. The spreading of deposited ink was studied by printing the ink on different substrate materials: stainless steel plate, slide glass, and inkjet film. Although the nozzle size was known to be about 30 µm, the actual size of the printed dot needed to be determined. The spreading of the ink is important when trying to get a precise deposition pattern in inkjet printing. This experiment was carried out to study the ink-spreading area on different materials when the same volume of ink was deposited, so that spacing for complement printing distance

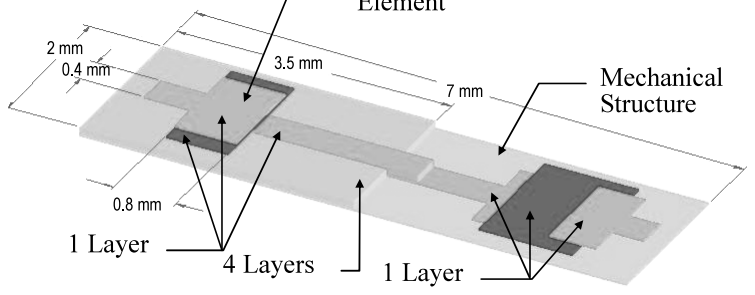
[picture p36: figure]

Fig. 7 Integration of mechanical and electrical elements in a part

can be established. The printed line width and its average roughness (Ra) were measured and recorded.
2. 4 Printing resolution
Resolution is a basic term used to classify printers and is most commonly expressed in dots per inch (dpi), denoting the number of clearly resolved points a printhead can theoretically print in a one-inch interval. Horizontal resolution is defined by the firing frequency of the printhead and the linear speed of its horizontal movement, while vertical resolution depends on the positioning accuracy of the mechanical paper feed. In this study, however, since the mechanical paper feed was removed and replaced by motorized stages, ink positioning accuracy on the vertical axis was determined by complement printing, or overlaying the ink between the two adjacent nozzles, which were 144 µm apart. Ra, a parameter for measuring the average roughness of a surface, was measured from 1 complement printing up to 11 complement printings.
2. 5 Printing 3D patterns
The ability of inkjet printing technology to arrange dots precisely to create layers of material makes it interesting in layering multiple materials integrated into one part. By printing layer by layer on top of one another, thicknesses of 1, 3, 5, 7 and 9 layers were recorded. In this study, experiments were also carried out to fabricate a part consisting of a mechanical structure and electrical elements, such as printing a schematic of a capacitor pattern on a surface of different heights using pigment ink for positional verification, as shown in Fig. 7.

### 3. Experimental Results

3. 1 Ink drying and spreading
From this simple experiment, the results show that increasing drying temperature reduces drying time, and at 80◦C the ink dries in about 10 seconds, as depicted in Fig. 8. Although we can use higher temperatures to shorten drying time, care must also be taken concerning the effect of heat on nozzle surfaces, to prevent ink drying and clogging the printhead nozzles. Heat should be just high enough to evaporate the solvents in the ink. The results shown in Fig. 9 indicate that ink printed on three different materials, stainless steel plate, slide glass and inkjet film, gave different spreading areas. The width of the line

357

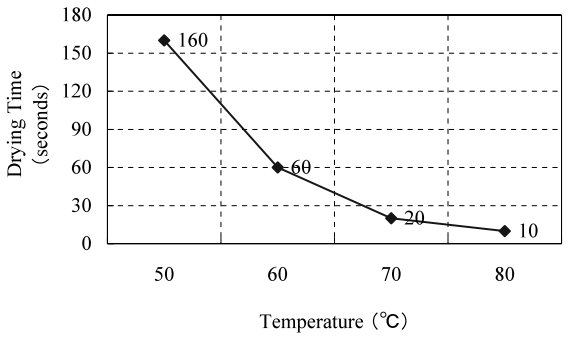
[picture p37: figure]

Fig. 8 Drying time

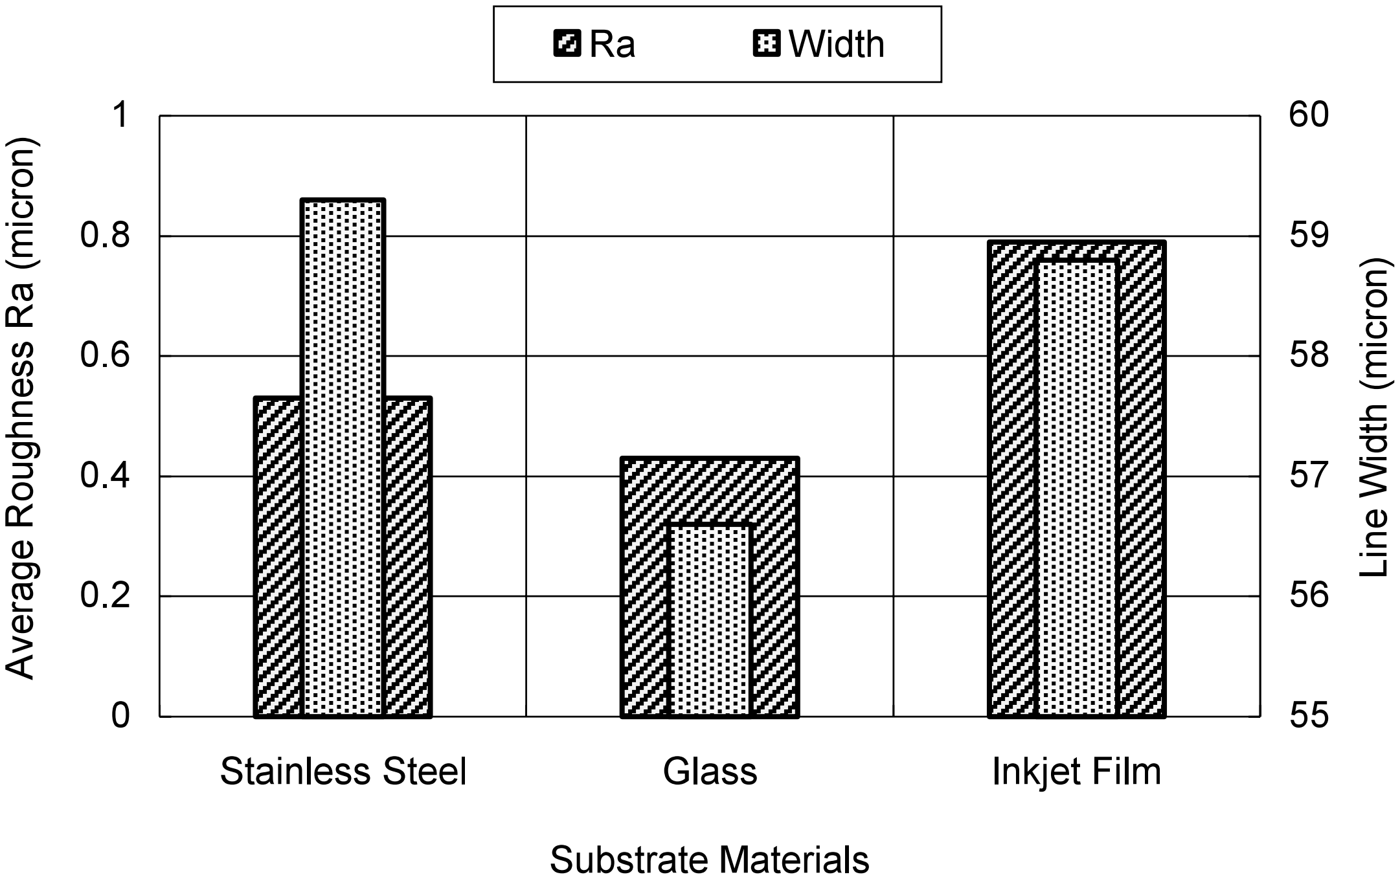
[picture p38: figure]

Fig. 9 Ink spreading

printed on glass is less than that of ink printed on stainless steel plate and inkjet film. This shows that the ink spread less on glass because its contact angle, which determines its wetting, is greater than ink printed on the other substrates. The average roughness value of ink printed on glass is also lower than the other materials.
3. 2 Printing resolution
Experiments were carried out to establish a fully dense deposition pattern by means of complement printing. Figure 10 (a) shows the result of printing without complement, with a gap of about 90 µm between the two adjacent nozzles. After one complement printing, the gap was still not fully covered by the ink, because the width of a dot is only about 55 µm, as shown in Fig. 10 (b). In order to fully fill the gap between the two adjacent nozzles a minimum of two complement printings 48 µm apart are necessary, as shown in Fig. 10 (c). With nozzle size 30 µm in diameter, nozzles 144 µm apart, and printed at a horizontal resolution of 360 dpi, the smallest a dot can be printed is about 55 µm horizontally and 150 µm vertically, which is from one pixel square image, as depicted in Fig. 11. Overlay printing until there are 11 complements between the two nozzles shows that the roughness of the surface increases as more lines were printed with smaller print spacing, as shown in Fig. 12.
For the layer thickness experiment, a 36 µm print spacing was used to print a square pattern, and differ-

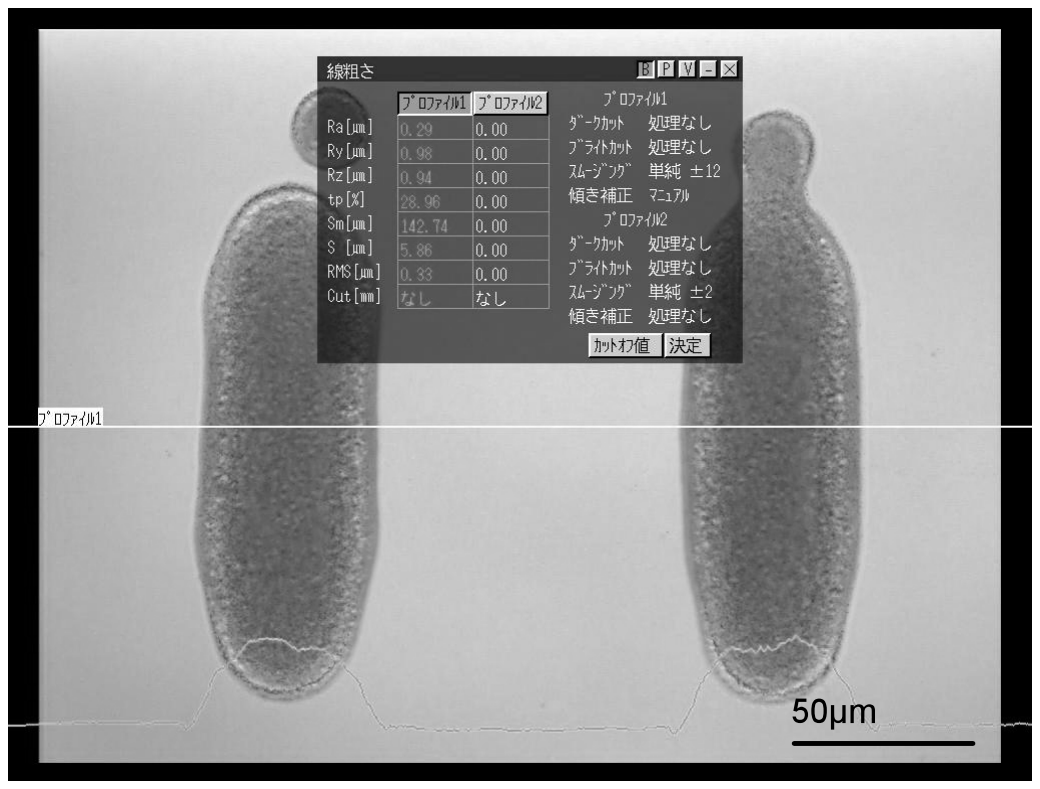
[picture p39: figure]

(a) Without complements

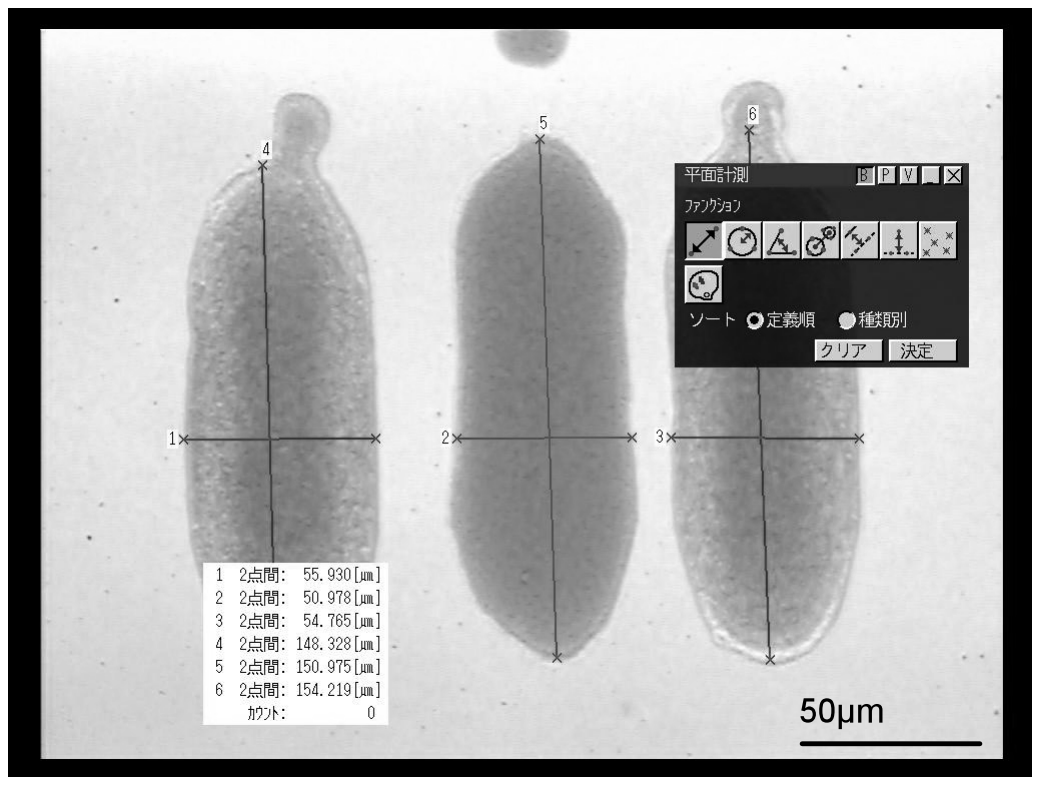
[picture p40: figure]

(b) One complement

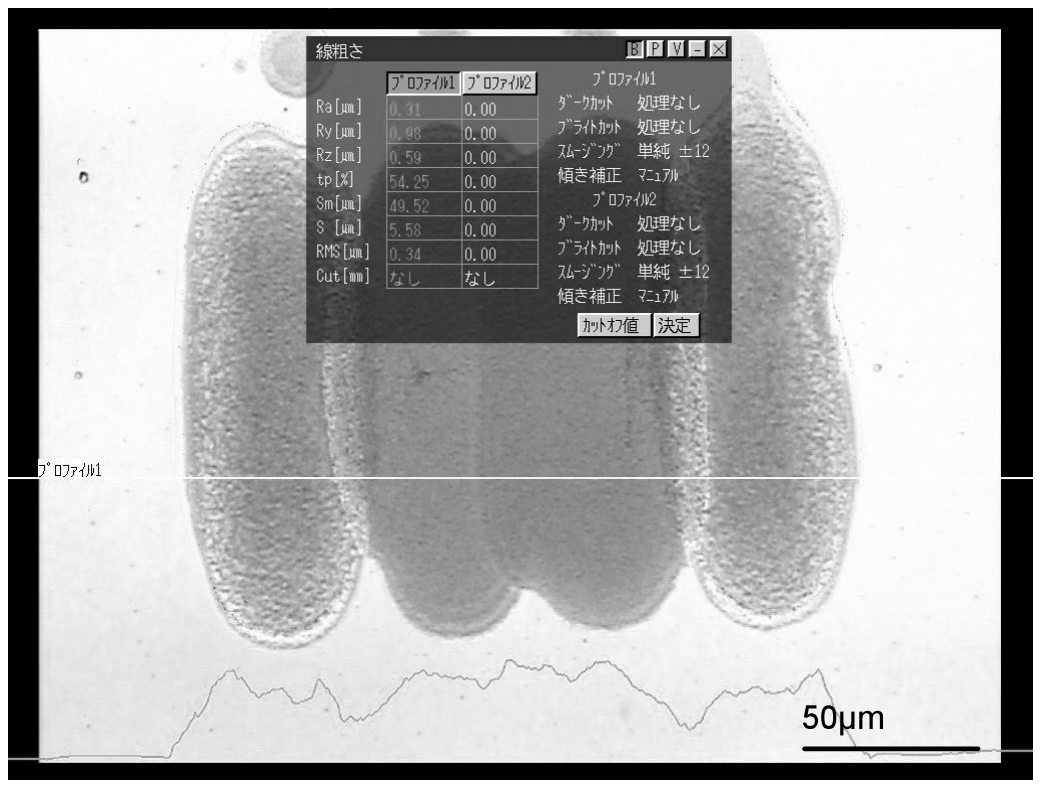
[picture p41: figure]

(c) Two complements

Fig. 10 Complement printing results

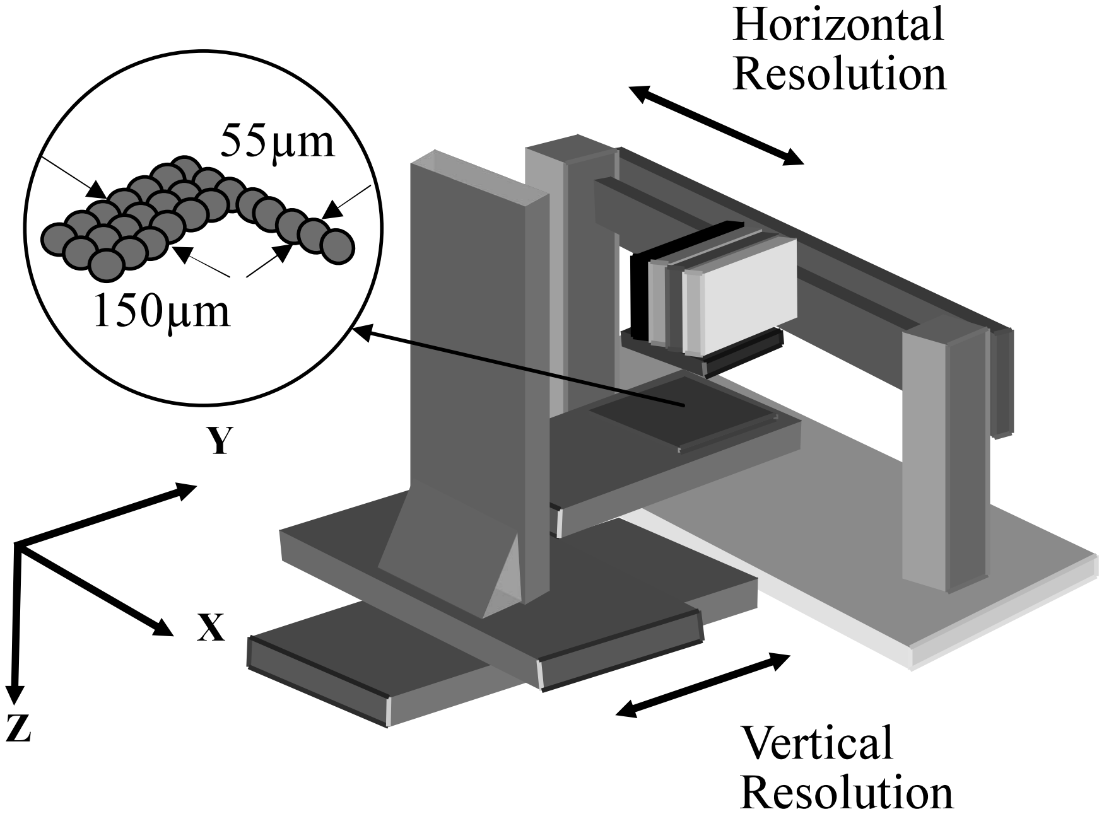
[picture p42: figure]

Fig. 11 Printing resolution

358

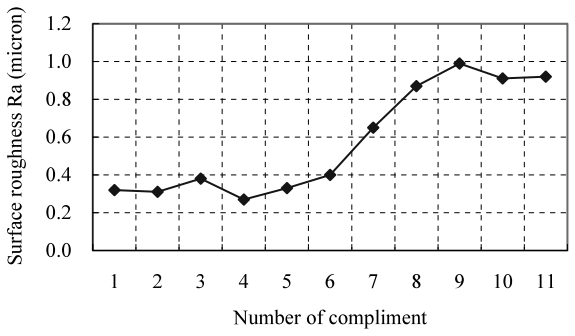
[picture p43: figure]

Fig. 12 Complements printing surface roughness

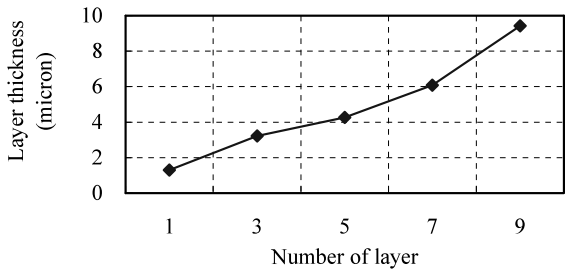
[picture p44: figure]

Fig. 13 Layer thickness

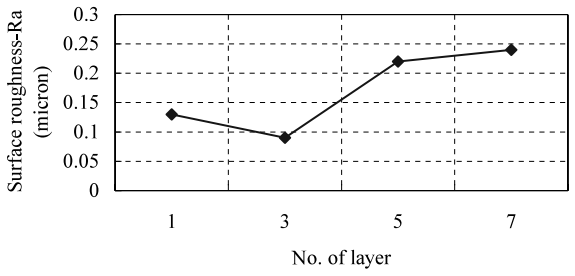
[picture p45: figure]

Fig. 14 Layer surface roughness

ences in thickness were measured. The results indicate that when the first layer was printed on the slide glass, the edge of the ink tended to spread on the glass surface. As the number of layers increased there was almost a linear increase in the average thickness of the pattern, as shown in Fig. 13. The surface roughness on different number of layers was also presented as shown in Fig. 14.
3. 3 Printing 3D patterns
For the experiment to print a capacitor pattern, described in Fig. 15 (a), two types of ink were used: cyan, representing conductive ink for the electrodes, and magenta, representing dielectric ink. The bottom electrode, dielectric and top electrode layers were laid down successively. Both the area and thickness of the dielectric could be varied to select the value of the capacitance. The 3D profile of the pattern was shown in Fig. 15 (b). For the second 3D pattern, the capacitor was printed on the surface of the mechanical structure, represented by the yellow ink. A structure with varying surface heights was fabricated

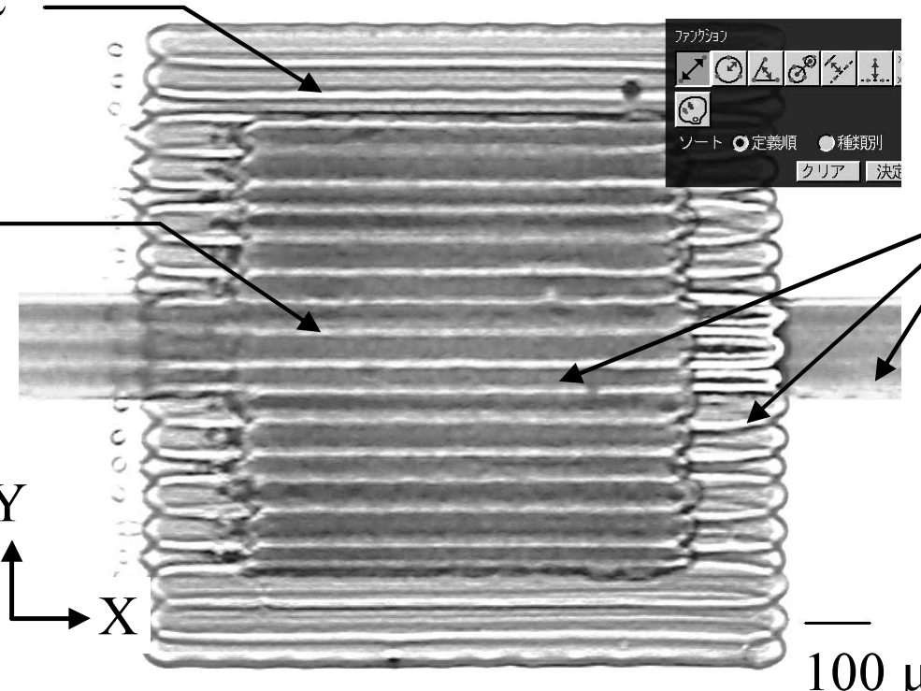
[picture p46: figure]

(a) Inkjet printing of capacitor model

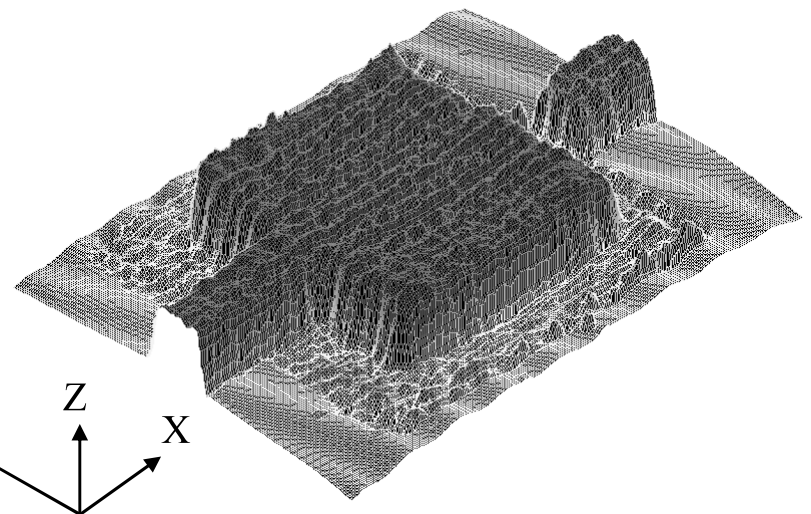
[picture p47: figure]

(b) 3D profile of capacitor model

Fig. 15 Capacitor patterns printing result

by printing different numbers of layers, with each layer roughly 1 µm thick. The images described in Fig. 16 show the use of inkjet printing to fabricate multiple material 3D patterns with reference to Rapid Prototyping technology, which fabricates 3D objects layer by layer.

### 4. Discussion

The ability to convert CAD design data and control an inkjet printing machine within a Java program gives us the flexibility to harmonize different equipment in the same environment. A commercial inkjet printer was modified and transformed into a machine that can fabricate 3D structures. Although there are still many improvements to be made in terms of hardware and software, the capability of the inkjet printing technology in depositing material layer by layer to build 3D structures is promising. Fabricating multi-material 3D structures using inkjet printing technology require arrangement and overlaying the deposited dots in a manner that will create a dense and flat layer pattern. The movement of the additional axes must be synchronized with the ink deposition rate so that we can direct write patterns with the deposited fluid.
From our experiment with nozzle size of 30 µm in diameter, 144 µm apart and printed at a horizontal resolution of 360 dpi, the smallest dot can be printed is about 55 µm horizontally and about 150 µm vertically which is from one pixel square image. The pixel image data need to be modified so that variable dot size can be chosen based on the size of the region that needs to be printed. The abil-

359

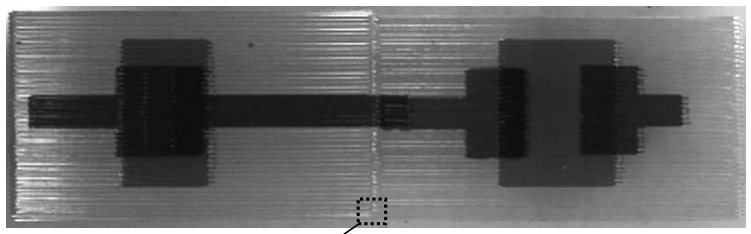
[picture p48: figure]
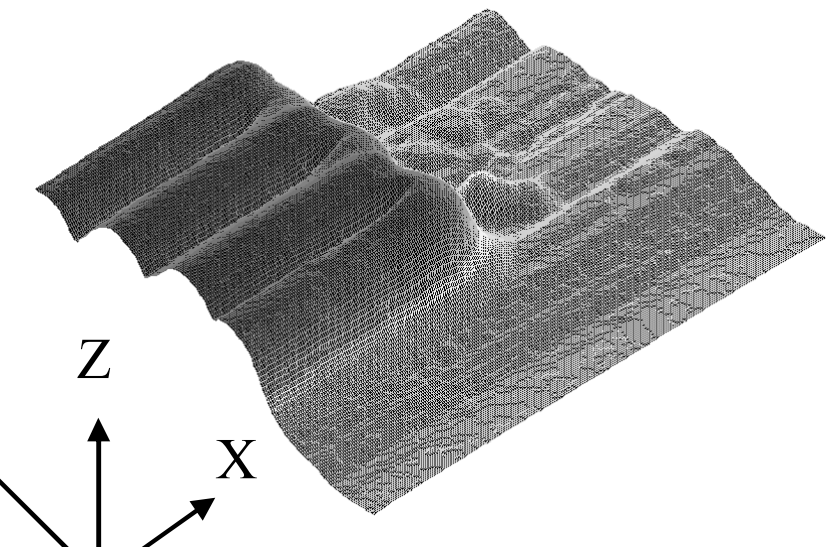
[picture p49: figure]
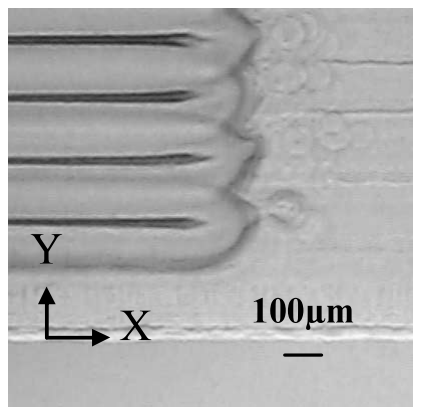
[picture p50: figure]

Fig. 16 Inkjet printing of part with capacitor model

ity of the program to control fluid deposition with different sizes will inevitably improve the print resolution because circular dots tend to leave void areas at their corners, making it difficult to fabricate sharp edges.
The nozzles must also be taken care of because heat interaction on fluid can clog nozzle openings. If particles clog parts of a nozzle, both horizontal and vertical resolution can be affected, and a deviation of 1 degree can cause dot misplacement of a few microns. This will also cause “satellite drops”, unwanted drops of ink that break off from the main droplets. A study of inkjet printing resolution using normal printing ink was necessary prior to printing with functional inks because fluids such as metalfilled conductive inks or polymer inks are not cheap, and extra care must be taken in handling these materials.

### 5. Conclusion

The ability to build multiple-material prototypes or models from a rapid prototyping machine will inevitably bring manufacturing technology to another dimension. The inkjet printing machine that we built shows flexibility in depositing fluid of multiple materials and in the number of complement printings needed to build 3D structures layer by layer using the Java program. The program can also be used to generate one ink cartridge (tool) path file for every different material to be deposited onto using inkjet printing technology. From the experiments done to explore ink deposition resolution using a commercial piezoelectric printer, a few conclusions can be made:
- When printing at a horizontal resolution of 360 dpi, the minimum width achievable is 55 µm in the X axis and about 150 µm in the Y axis.
- The minimum complement printing distance necessary to connect dots in the Y axis is about 48 µm, which is 2 complement printings between nozzles 144 µm apart.

References

( 1 ) Wallace, D.B. and Hayes, D.J., Solder JetTM-Optics JetTM-AromaJetTM-Reagent Jet-Tooth Jet and other Applications of Ink-Jet Printing Technology, Proceedings, NIP18: International Conference on Digital Printing Technologies, San Diego, CA, Sept. 29, (2002).
( 2 ) Grimm, T. and Wohlers, T., Time Compression Technologies, May, (2001).
( 3 ) Wallace, D.B., Cox, W.R. and Hayes, D.J., Direct Write for Ink-Jet Techniques, Edited by Pique, A. and Chrisey, D.B., Direct Write Technologies for Rapid Prototyping Applications-Sensors, Electronics, and Integrated Power Sources, (2002), Academic Press, New York.
( 4 ) Hayes, D.J., Cox, W.R. and Wallace, D.B., Printing System for MEMS Packaging, Proceedings, SPIE Micromachining & Microfabrication Conference, San Francisco, CA, October 22-25, (2001).
( 5 ) Shah, V.G. and Hayes, D.J., Trimming and Printing of Embedded Resistors Using Demand-Mode Ink-Jet Technology and Conductive Polymer Proc. IPC Printed Circuits Expo 2002, Long Beach, CA, March 24-28, (2002).
( 6 ) Cooley, P.W., Wallace, D.B. and Antohe, B.V., Application of Ink-Jet Printing Technology to BioMEMS and Microfluidic Systems, Proceedings, SPIE Microfluidics and BioMEMS Conference, San Francisco CA, October 22-25, (2001).
( 7 ) Elliott, L., Rapid Manufacturing Ramps Up, Desktop Engineering, November, (2004).
( 8 ) Conjoined Twins’ Operation Planned Using the Objet Quadra Tempo RP System. Retrieved 05 September 2002. http://www.2objet.com.
( 9 ) Zhu, W.-M. and Yu, K.-M., Tool Path Generation of Multi-Material Assembly for Rapid Manufacture, Rapid Prototyping Journal, Vol.8, No.5 (2002),

360

pp.277–283.
(10) Mustaffa, B.I., Narahara, H., Koresawa, H. and Suzuki, H., Integration of Silver Nanoparticle Inkjet Printing and Layered Manufacturing Technology, Proc the 7th. Intl. Conf. Quality in Research (QIR) 2004 (Mech. Engineering), ME-DM-04-1-4, Jakarta, Indonesia, August, (2004).
(11) Mustaffa, B.I., Narahara, H. and Suzuki, H., Electronic Circuit Fabrication Using Inkjet Printed Silver Nanoparticles for SFF, Proc. of Japan Society for Precision Engineering National Conference, Tokyo, (2004), pp.83–84.
(12) McGill, R.A., Ringeisen, B. and Wu, P.K., The Role of Direct Writing for Chemical and Biological Materials: Commercial & Military Sensing Applications, Edited by Pique, A. and Chrisey, D.B., Direct Write Technologies for Rapid Prototyping Applications-Sensors, Electronics, and Integrated Power Sources, (2002), Academic Press, New York.

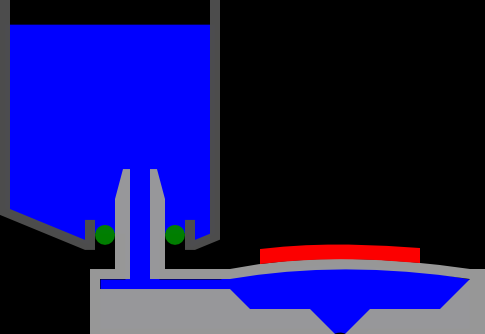
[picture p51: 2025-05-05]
photos/printhead-in.png

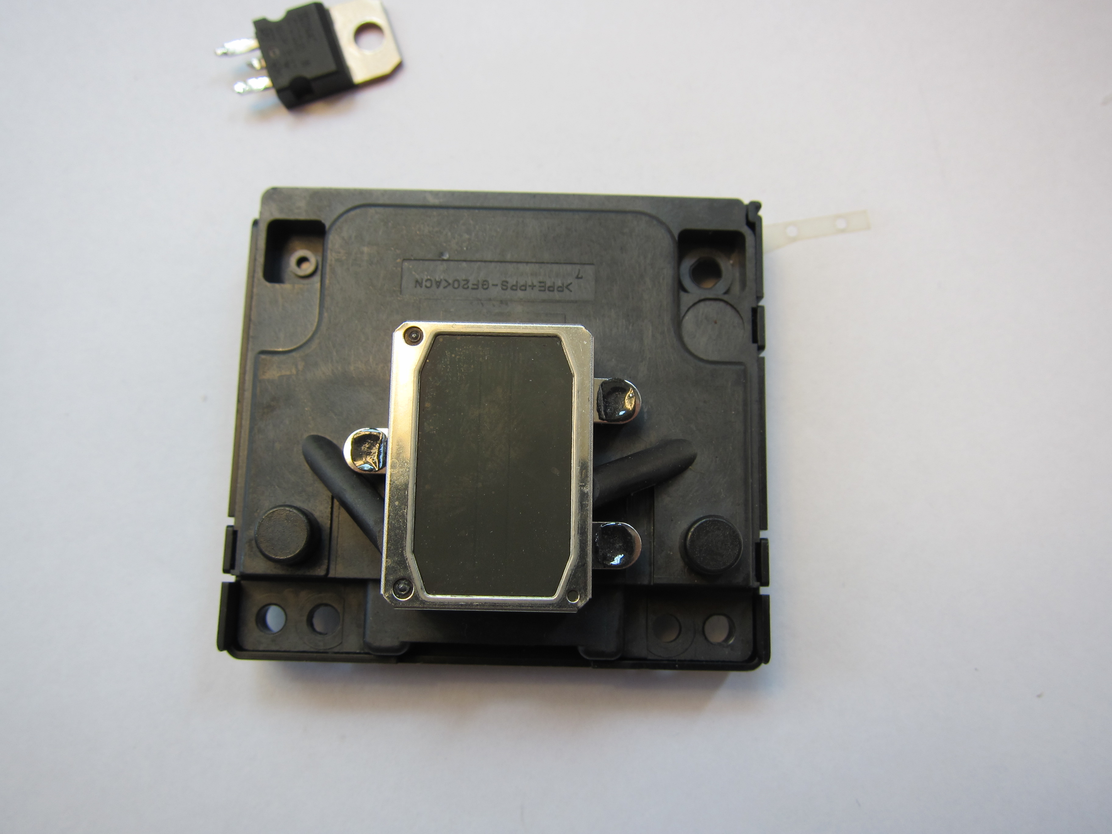
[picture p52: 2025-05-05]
photos/s21-printhead-bottom.JPG

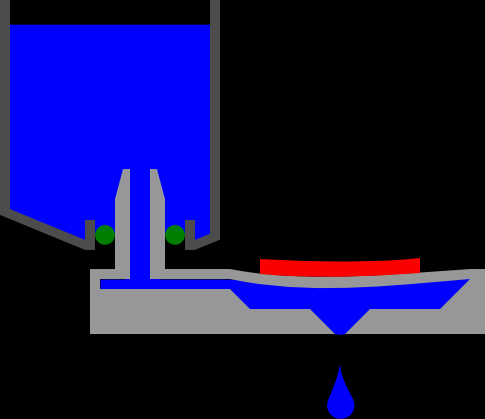
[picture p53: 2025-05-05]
photos/printhead-out.png

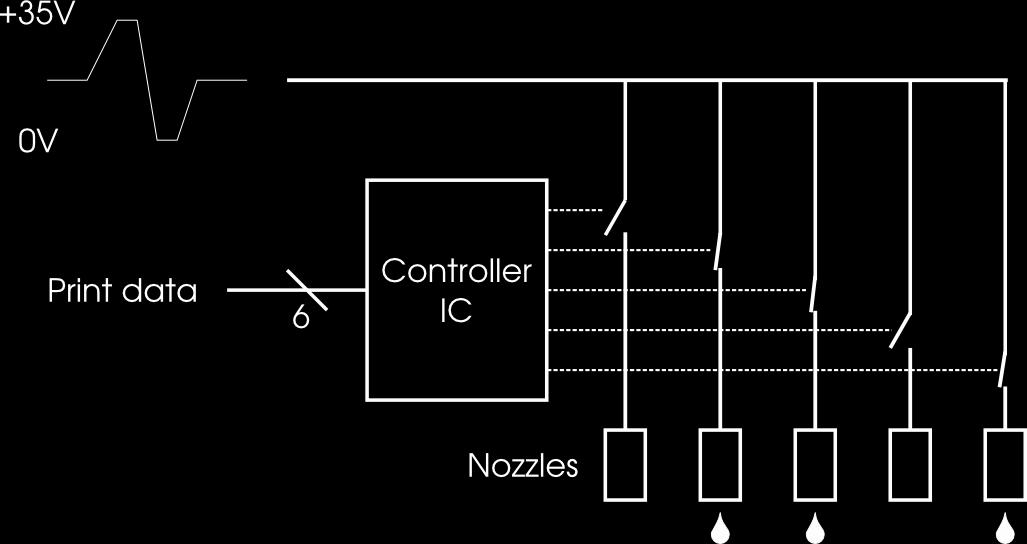
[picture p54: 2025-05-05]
photos/printheadinterface.png

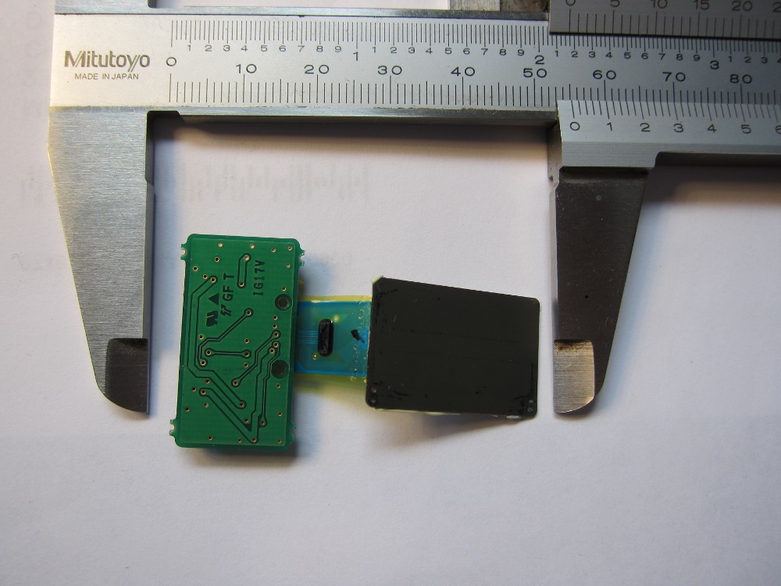
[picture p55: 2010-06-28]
photos/printhead-top.jpg

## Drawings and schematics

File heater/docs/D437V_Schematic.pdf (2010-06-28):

# D437 LCD Demo

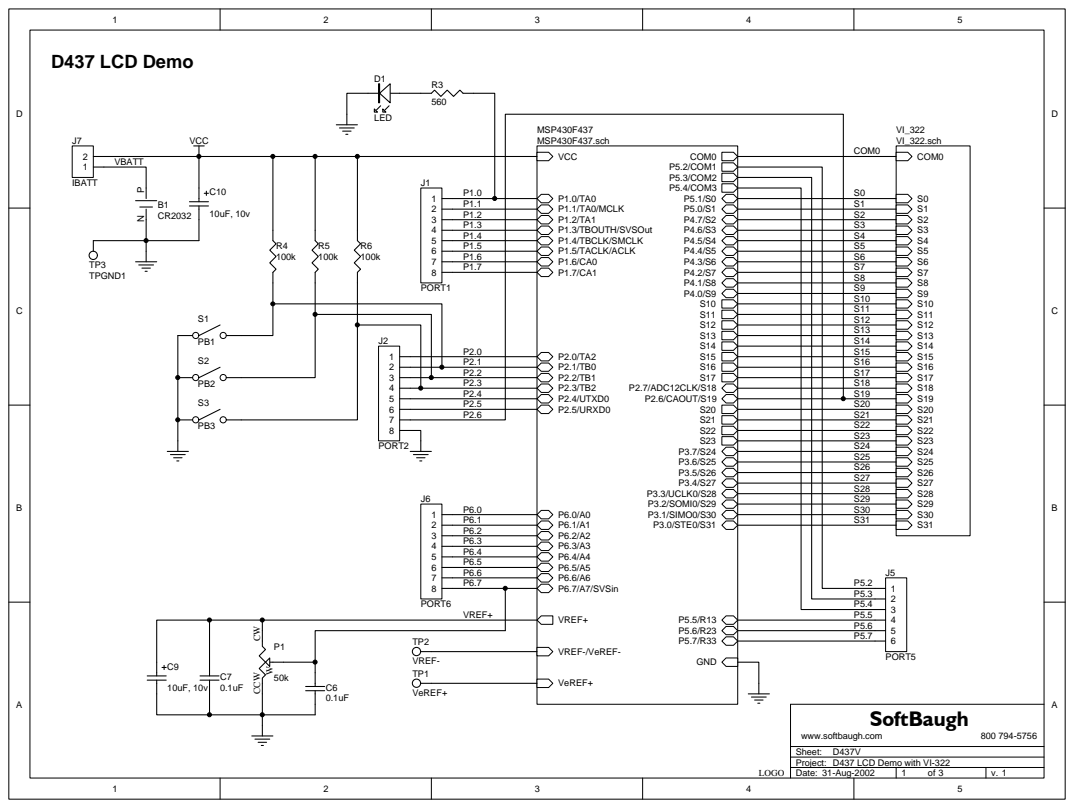
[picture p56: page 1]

VI-322

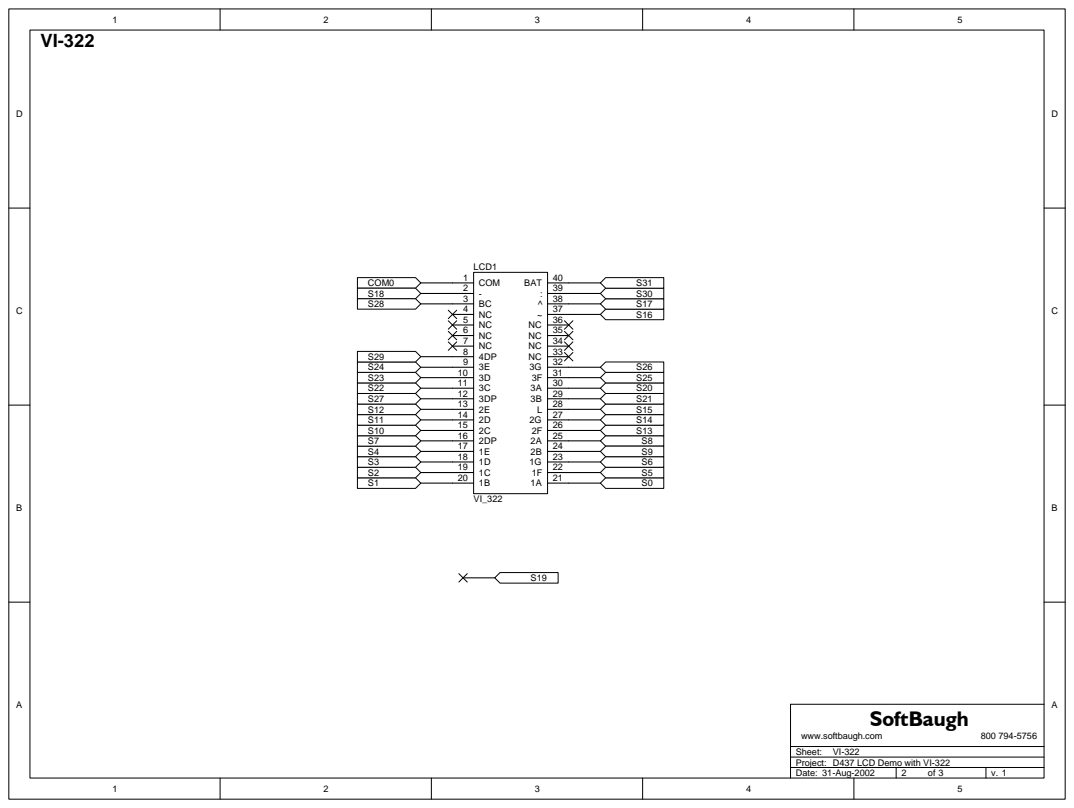
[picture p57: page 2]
ABCD; DCBA; www.softbaugh.com; Project:; Date:; Sheet:; SoftBaugh; COM0; COM; 39 BAT 40; LCD1

D437 LCD Demo with VI-322
31-Aug-2002

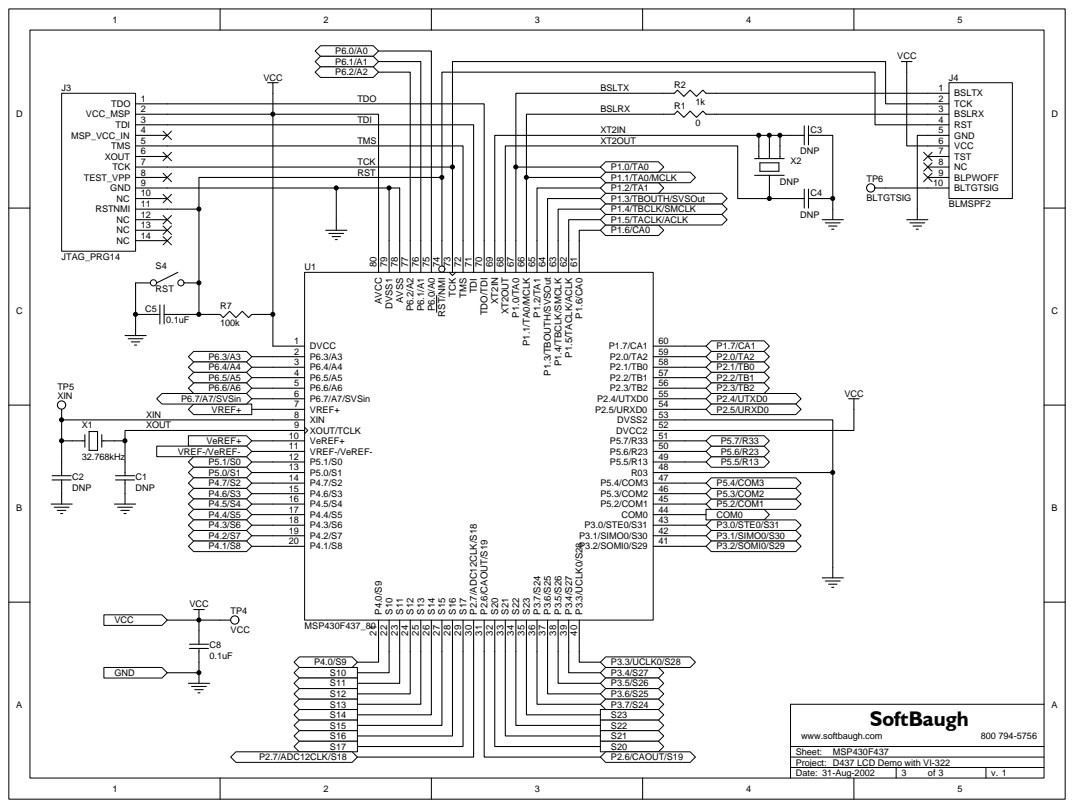
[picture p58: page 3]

TDO/TDI 70 TDI 71 TMS 72 TCK 73 RST/NMI 74 P6.0/A0 75

P1.6/CA0 61 P1.5/TACLK/ACLK 62 P1.4/TBCLK/SMCLK 63

MSP430F437
D437 LCD Demo with VI-322

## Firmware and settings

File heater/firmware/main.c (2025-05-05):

/*
 * Copyright (c) 2025 Jeff Gough
 *
 * This software is released under the MIT License.
 * See the LICENSE file for full license text.
 */

#include <signal.h>
#include <msp430x43x.h>

#include "lcd.h"
#include "adc.h"
#include "pwm.h"

void init(void);

//gdb bug fix - falls over if there is an empty .data section
static unsigned int dummy=1;


unsigned char p_pid = 0;

interrupt (PORT2_VECTOR) port2isr(void)
{
  if (P2IFG & 1<<1) //button 1 pressed
    //    bees++;
  if (P2IFG & 1<<2) //button 2 pressed
    //be/es--;
  if (P2IFG & 1<<3); //button 3 pressed
    
  P2IFG=0;//interrupts handled, clear flags
  // lcdvalue(bees);
}


//Fires at 400Hz (CCR0 timer reset)
interrupt (TIMERA0_VECTOR) pwm_periodinterrupt()
{
  #define SETPOINT 700
  static uint16_t counter = 0;
  uint16_t temperature = 0; // temperature = degrees C *10. Eg 300 = 30 degrees C

  uint8_t kp = 60;
  uint8_t ki = 5;
  uint8_t kd = 80;
  static int32_t perror = 0;
  static int32_t ierror = 0;
  static int32_t derror = 0;  
  static int32_t prev_perror = 0;
  static uint8_t itimeout = 90;
  static uint8_t dtimeout;
  static int32_t pid = 0;
  static int32_t pwmout = 0;
 
  if (counter++ == 40)
    {
      counter = 0;
      // Every 100ms...      
      temperature = (uint16_t)((uint32_t)(adc_getaverage()) * 2500 / 4095);
      
      //display temperature
      lcd_dispvalue((uint16_t)temperature);

      perror = (int32_t)SETPOINT - temperature;
      derror = perror - prev_perror;
      if (itimeout++ == 100)
	{
	  if ((pwmout != PWM_MAX) && (pwmout != PWM_MIN))
	    ierror += perror;
	  itimeout = 0;
	}
      if (dtimeout++ == 50)
	{
	  prev_perror = perror;
	  dtimeout = 0;
	}

      pid = (kp * perror) + (ki * ierror) + (kd * derror); 
      pwmout = pid;
      if (pwmout > PWM_MAX)
	pwmout = PWM_MAX;
      if (pwmout < PWM_MIN)
	pwmout = PWM_MIN;

      pwm_set((uint16_t)pwmout);
    }
  
  TACCTL0 &= ~CCIFG;
}


int main(void) 
{
  unsigned long vin=0;
   
  //PID variables
  signed long perror = 0;
  signed long prev_perror = 0;
  signed long ierror = 0;
  signed long derror = 0;
  volatile signed long kp = 30;
  signed long ki = 4;
  signed long kd = 20;
  signed long pterm = 0;
  signed long iterm = 0;
  signed long dterm = 0;
  signed long pid = 0;
  signed long new_pwmout = 0;
  unsigned int pid_div = 30;
  
  unsigned int itimer = 0;
  unsigned int itimeout = 1;
  unsigned char dtimer = 0;
  unsigned char dtimeout = 1;
  unsigned char lcdtimer = 0;
  unsigned char lcdtimeout = 50;

  unsigned char pwm_min = 0;
  unsigned int pwm_max = 270;

  unsigned char nowind = 0;
    
  unsigned char dead = 4;

  unsigned char bias=0;

  init();
  lcd_clear();

  while (1) 
    {
      P1OUT ^= 1;
    }

}


void init(void)
{
  //clock setup
  //with DCOPLUS=1, Fdcoclk = D * (N+1) * Faclk
  FLL_CTL0 = XCAP18PF | DCOPLUS; //set up crystal load caps and FLL division
  FLL_CTL1 = 0;  
  //we're driving aclk from 32kHz crystal. N=60, D=4 gives operating freq of Fdcoclk = 7995392
  SCFQCTL = 60;
  SCFI0 = FN_4 | FLLD_4;
  
  //disable watchdog timer
  WDTCTL = WDTPW| WDTHOLD;
  
  //port function select registers.
  P1SEL = 0x0e;
  P2SEL = 0x10;


  //port direction registers
  P1DIR  = 0x04 | (1<<0);
  P2DIR  = 0x10;

  //interrupt on button press on port 2
  P2IE   = 0x0e;

  //disable interrupts
  dint();

  //initialise other modules
  lcd_init();
  adc_init();
  pwm_init();
  //  uart_init();
  
  eint(); //enable interrupts
}

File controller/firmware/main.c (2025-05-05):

/*
 * Copyright (c) 2025 Jeff Gough
 *
 * This software is released under the MIT License.
 * See the LICENSE file for full license text.
 */

#include "device.h"
#include "stepper.h"
#include "wavegen.h"
#include "printhead.h"
#include "print.h"
#include "buttons.h"
#include <signal.h>
#include "/usr/msp430/include/msp430/svs.h"

/* Initialises everything. */
void init(void);

int dummy = 0;

void cleancycle()
{
  uint8_t i,j,k;
  for (j=0;j<K_NOZZLES;j++)
    {
      for (i=0;i<K_NOZZLES;i++)	/* clear all nozzles */
	bk_data[i] = 0;
      //     bk_data[j] = 1;
      printhead_period();
      
      for (k=0; k<50; k++)
	wavegen_cleanpulse();
    }
}

int main( void )
{
  volatile uint32_t j,i,k, drops, steps;
  uint8_t nozzle =0;
  uint8_t startprint = 0;
  uint8_t leds,dir;

  init();
  P5DIR = 0xff;
  P5OUT &= 0x0f;

  stepper_setxvelocity(0, 0);

  while (startprint == 0)
    {
      i = 100000;
      while ( (startprint == 0) && (i > 0))
	{
	  startprint = buttons_getstate();
	  i--;
	}

      P5OUT ^= (1<<4);
    }
  if (buttons_getstate() & (1<<0))
    {
      jobstate = JOB_TEST;
      P5OUT &= 0x0f;
      P5OUT |= 12<<4;
    }
  else
    {
      jobstate = JOB_NORMAL;
      P5OUT &= 0x0f;
      P5OUT |= 3<<4;
    }    

  stepper_enable(Y_MOTOR);
  stepper_xhome();
  print_image();
  stepper_xhome();

  while(1);

  while (1)
    {
      //      print_cleancycle();
      //      for (i=0; i<5; i++)
      //	{
	  //	  print_nozzle_test();
      //	  print_line();
	  //	}
    }
}

void init(void)
{
  /* GPIO: All inputs */
  P1DIR = P2DIR = P3DIR = P4DIR = P5DIR = P6DIR = P7DIR = P8DIR = 0;
  P8SEL=0;
  
  /* Disable the watchdog timer */
  WDTCTL = WDTHOLD | WDTPW;

  /* Use a 16 MHz clock (DCO) */
  DCOCTL = CALDCO_16MHZ;
  BCSCTL1 &= ~0x0f;
  BCSCTL1 |= 
    /*XT2O=0: XT2 is on*/
    /*XTS=0: LFXT1 mode select. 0 -Low frequency mode*/
    DIVA_0 /* ACLK Divider 0: /1 */
    | CALBC1_16MHZ; /* BCSCTL1 Calibration Data for 16MHz */
  
  BCSCTL2 = SELM_DCOCLK	/* MCLK from DCO */
    /* DIVMx = 0 : No MCLK divider */
    /* SELS = 0: SMCLK from DCO */
    | DIVS_DIV1 /* : Divide SMCLK by 1
*/
    /* DCOR = 0 : DCO internal resistor */;

  //  SVSCTL = VLD_3 | PORON;		/* SVS at 2.2V */
  
  buttons_init();
  wavegen_init();
  printhead_init();
  stepper_init();

  stepper_disable(X_MOTOR);
  stepper_enable(X_MOTOR);
  eint();
}

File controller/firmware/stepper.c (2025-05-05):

/*
 * Copyright (c) 2025 Jeff Gough
 *
 * This software is released under the MIT License.
 * See the LICENSE file for full license text.
 */

#include "device.h"
#include "stepper.h"
#include "print.h"
#include <signal.h>

#define EN (1<<0)
#define CONTROL (1<<1)
#define HF (1<<2)
#define DIR (1<<3)
#define CLOCK (1<<4)
#define nRESET (1<<5)

volatile uint16_t carriagepos;
uint8_t xstate;

/* Motor 0 is the right-hand driver, black connector. */
/* Motor 1 is the left-hand driver, red connector. */


void stepper_init()
{
  carriagepos = 1000;
  xstate = 0;

  P1DIR |= EN | CONTROL | HF | DIR | CLOCK | nRESET;
  P2DIR |= EN | CONTROL | HF | DIR | nRESET;
  P1OUT |= HF;   			/* Fast decay, half step */
  P2OUT |= HF;
  
  TACTL = 
    TASSEL_SMCLK 		/* Clock TA from SMCLK =16MHz */
    | ID_DIV8			/* /8 = 2MHz */
    | MC_UPTO_CCR0		
    | TAIE;

  TACCR0 = 40000;		/* 50Hz to start with... */
  TACCTL0 = OUTMOD_TOGGLE;	/* Toggle TA0 (P2.7) with TA overflow (clocks X stepper)*/
  P2SEL |= (1<<7);
  P2DIR |= (1<<7);

  P6DIR &= ~(1<<5);
  P6REN |= (1<<5);		/* Enable pull up resistor on the home switch */
  P6OUT |= (1<<5);		/* Pull _up_ */
  
  P5DIR |= (1<<3);
}

void stepper_xhome()
{
  volatile uint16_t i = 0;

  stepper_setxvelocity(SPEED_SLOW, CARRIAGE_RIGHT);
  while ( !stepper_ishome() )
    i++;
 
  stepper_setxvelocity(0, 0);
  carriagepos = 0;
}

void stepper_moveXto(uint16_t newpos, uint16_t speed)
{
  if (newpos > carriagepos)
    stepper_setxvelocity(speed, CARRIAGE_LEFT);
  if (newpos < carriagepos)
    stepper_setxvelocity(speed, CARRIAGE_RIGHT);
  
  while (carriagepos != newpos);

  stepper_setxvelocity(0,0);
 }

void stepper_setxvelocity(uint16_t interval, uint8_t direction)
{
  if (interval == 0)
    {
      stepper_disable(X_MOTOR);
      xstate = STOPPED;
    }
  else
    {
      stepper_enable(X_MOTOR);
      if (direction)
	{
	  xstate = CARRIAGE_LEFT;
	  P2OUT |= DIR;
	}
      else
	{
	  xstate = CARRIAGE_RIGHT;
	  P2OUT &= ~DIR;
	}
      TACCR0 = interval;
    }
}

interrupt (TIMERA1_VECTOR) stepper_stepinterrupt(void)
{
  static uint8_t level = 0;
  P5OUT |= (1<<3);

  level ^= 1;
  if (level) {
    /* 
     * interrupt fires on every transition, resulting in 2 print_process calls
     * per step.  This if lets only half pass
     */
    return;  
  }

  switch (xstate)
    {
    case CARRIAGE_LEFT:
      carriagepos++;
      break;
    case CARRIAGE_RIGHT:
      carriagepos--;
      break;
    }

  print_nextpixel();
  TACTL &= ~TAIFG;
  P5OUT &= ~(1<<3);
}


void stepper_Ystep( uint8_t direction, uint8_t steps)
{
  volatile uint8_t count, i;
  if (direction)
      P1OUT |= DIR;
  else
      P1OUT &= ~DIR;

  for (count = 0; count < steps; count++ )
    {
      P1OUT |= CLOCK;
      for (i = 0; i < 5; i++);
      P1OUT &= ~CLOCK;

      for (i=0; i<255; i++);	/* Delay to allow stepper to move */
    }
}

void stepper_xstep( uint8_t direction)
{
  volatile uint8_t count;
  if (direction)
    {
      P2OUT |= DIR;
      P2OUT |= CLOCK;
      for (count = 0; count < 5; count++);
      P2OUT &= ~CLOCK;
    }
  else
    {
      P2OUT &= ~DIR;
      P2OUT |= CLOCK;
      for (count = 0; count < 5; count++);
      P2OUT &= ~CLOCK;
    }
}

void stepper_enable(uint8_t motor)
{
  if (motor == 0)
    {
      P1OUT |= EN;
      P1OUT |= nRESET;
    }
  if (motor == 1)
    {
      P2OUT |= EN;
      P2OUT |= nRESET;
    }
}

void stepper_disable(uint8_t motor)
{
  if (motor == 0)		/* Y */
    {
      P1OUT &= ~EN;
      P1OUT &= ~nRESET;
    }
  if (motor == 1)		/* X */
    {
      P2OUT &= ~EN;
      P2OUT &= ~nRESET;
    }
}


uint16_t stepper_getXpos() 
{
  return carriagepos;
}

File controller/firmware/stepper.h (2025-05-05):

/*
 * Copyright (c) 2025 Jeff Gough
 *
 * This software is released under the MIT License.
 * See the LICENSE file for full license text.
 */

#ifndef __STEPPER_H
#define __STEPPER_H

#define SPEED_SLOW 4000
#define SPEED_CLEAN 8000
#define SPEED_NORMAL 1000
#define SPEED_PRINT 1200

#define X_MOTOR 1
#define Y_MOTOR 0
#define CARRIAGE_LEFT 1
#define CARRIAGE_RIGHT 0
#define PAGE_FORWARDS 0
#define PAGE_BACKWARDS 1
#define STOPPED 3

extern volatile uint16_t carriagepos;

#define stepper_ishome() (P6IN & (1<<5) ? 0 : 1)
void stepper_init();
void stepper_enable(uint8_t motor);
void stepper_disable(uint8_t motor);
void stepper_setxvelocity(uint16_t speed, uint8_t direction);
void stepper_moveXto(uint16_t newpos, uint16_t speed);
void stepper_Ystep( uint8_t direction, uint8_t steps);

void stepper_xhome();
uint16_t stepper_getXpos();



#endif

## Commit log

2010-06-07 started work on a tool to fool the paper sensor in the epson 680, using an ez430 2313 daughterboard
2010-06-07 set up 10hz interrupt using timer a
2010-06-23 pcb design for heater board. prepared bmp file for laser etching
    [heater.brd, heater.sch]
2010-06-24 pcb routing finished. board made as per heater.bmp
    [heater.brd]
2010-06-25 added capacitor to feedback of the control amp and a resistor on the output of the current sense amp. these measures prevent the circuit from oscillating (too much gain)
    [heater.brd, heater.sch]
2010-06-26 added docs
    [heater.brd, heater.sch]
2010-06-27 imported code from 3rd year project to drive the d437 dev board's lcd. edited makefile to strip out some files
2010-06-27 pid loop now working. tuned roughly, performs pretty well. heats to 70 degrees from room temperature in around 1 minute with 1.5 degree overshoot
    [heater.brd, heater.sch]
2010-06-27 added printhead cad. about to laser ablate the residual silicone and cut some double-sided tape gaskets
    [tape.dxf]
2010-06-27 accidentally had the hole placement in the tape gasket mirrored
2010-06-28 added pores to the printhead design, and clearance for the pores in the tape layer
2010-06-28 added some heater docs
2010-06-28 oops, hadn't added the adc firmware files
2010-06-28 photos of the printhead
2010-06-28 new pcb layout for prototype printhead control electronics (msp430 based)
    [heater.brd, heater.sch, proto.brd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]
2010-06-28 bmp export of tqfp 40, 0.2mm pitch, to test laser ablation
2010-06-28 made description file. rotated part 45 degrees so that neither major axis of the tracks runs parallel to the engraving direction (tracks perpendicular to engraving direction appear to be etched sligh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
    [proto.brd, tape.dxf]
2010-06-28 added library file for controller pcb. made a device for the e0941ra epson dac/amp chip
    [proto.sch]
2010-06-29 added ffc and drive transistors to lib. captured schematic for adc. current amp and ffc connector
    [proto.sch]
2010-06-29 docs for control board!
2010-06-29 added bom. more schematic design
    [proto.brd, proto.ods, proto.sch]
2010-06-30 schematic finished. ready for routing. added datasheet for dc-dc converter module
    [proto.brd, proto.sch]
2010-06-30 added a couple of test points and notes
    [proto.brd, proto.sch]
2010-06-30 routed most of a motor driver block
    [proto.brd]
2010-06-30 more routing of motor controller
    [proto.brd]
2010-06-30 more routing
    [proto.brd, proto.sch]
2010-07-02 reduced track widths around msp from 0.3 to 0.2mm. passes pcbtrain express drc
    [proto.brd, proto.sch]
2010-07-02 added prototyping area to controller prototype pcb. produced gerbers, and ordered production by pcb train.
    [proto.brd]
2010-07-02 datasheet for stepper driver
2010-07-02 imported dma code from heart project
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2010-07-02 implemented the start of a dma-based waveform generator. this should output a ramp signal, complete with latching pulses on P1.6. Unfortunately, I didn't think about how the DACLAT signal would be ge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
    [main.c]
2010-11-10 dac is producing a nice trapezium wave. running at full speed with correct timing per recorded traces of epson's trapesia
    [main.c]
2010-11-21 remove anything to do with the psave pin - I think it's an output from the dac, and need not be touched.
2010-11-21 move dma config before dma enable
2010-11-21 wow, printing works amazingly well with reduced duty cycle of drive signal
2010-11-21 created the printhead control bitbanging module
2010-11-21 firing a single nozzle. almost works, but the low nozzle numbers, maybe below about 20, aren't firing. must have the data format incorrect somehow
2010-11-22 docs, etc
    [heatertop.dxf]
2010-11-23 played with greytable, can't get printhead to behave completely. on the plus side, wax prints beautifully.
2010-11-23 added note regarding lm358. previously been using a lm358 with no problems. just blew it up, and dont have spares, so am replacing it with a tsv358, which is the same, but rail-rail
    [heater.sch]
2010-11-25 added missing vref filter caps, enlarged holes on epson pin headers
    [proto.brd, proto.sch]
2010-11-25 moved sense resistors nearer to stepper drivers, widened their connections, and optimised and thickened routing of the traces to the motor connectors
    [proto.brd, proto.sch]
2010-11-29 added documents on the physical construction of the printhead, most notably hot bar reflow soldering
2010-11-29 made a start on the stepper code. printer now prints lines
2010-12-04 redesigned and machined another printhead. hopefully less leaky due to extra aluminium around the nozzle interfaces.
2010-12-07 track back and forth firing all nozzles
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2010-12-16 starting to improve the motion control. set up timer A to count at 2MHz. it's reset when it hits CCR0, and toggles its output pin. currently configured for 25Hz output freq. going to use this to cloc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
    [main.c, stepper.c, stepper.h]
2010-12-16 implemented home switch. carriage now homes on boot2
2010-12-16 fixed bug in setdir
    [stepper.c]
2010-12-16 added position tracking. can now move carriage to arbitrary position. home = 0, carriage increments to the left, decrements to the right. increments twice per step due to toggling nature of ccr0 deri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
2010-12-21 scan print head back and forth, squeegee every 5 passes
2010-12-21 oops, forgot to add these. high level choreography of the printing process.
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2010-12-21 Reset nozzle data before firing
    [print.c]
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2010-12-21 y stepper working. no code changes, just soldering.
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2010-12-21 Added margins to test nozzle and print image
2010-12-22 starting to merge in bodge. by hand
    [stepper.c]
2010-12-22 incorporate bodge to drive epson cadaver
    [main.c, stepper.c]
2010-12-22 changed a lot of things. mostly fixed warnings.
    [main.c, stepper.c]
2010-12-22 comment out everything to do with y axis bodge
    [stepper.c]
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2010-12-22 got rid of horrible stepper y bodge test code. now stepping properly in Y. turned out to be a soldering problem
    [main.c, stepper.c]
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2010-12-22 major refactoring to simplify image reading, printing process and raster processing
2010-12-22 compute X from current carriage location, including margins, etc.
2010-12-22 think it may be printing an image. the getpixel function was failing with the large numbers; needed some casting
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2010-12-23 Increase compression further by removing duplicate rows
    The MSP uses the "row_offset" array to discover where to find the
    beginning of the array in memory. This patch makes img2c.py look to
    see if we've already output a row that's identical to the one we're
    currently examining. If we have, then it simply references that one
    in the row_offset array instead of outputting new data.
2010-12-23 currently behaving quite well. etched a PCB, but wax not quite thick enough...
2010-12-23 switched to 4x subpixel greytable. output looking nice for now
2010-12-24 image data for peace logo. now printing well.
2010-12-25 added buttons. printer now waits for button press before printing
2025-05-05 Add photos
    [gasket-mask-mirrored-2.dxf, gasket-mask-mirrored-3.dxf, gasket-mask-mirrored.dxf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]
2025-05-05 Move BOM folder
    [proto.ods]
